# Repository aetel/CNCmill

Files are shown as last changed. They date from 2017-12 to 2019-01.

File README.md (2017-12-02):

# CNCmill
CNC mill based on the Sienci Mill One

## AETEL version

Frame has been modified to be cut from 4mm steel

## Shoulder of giants

The Mill One utilizes the following open-source projects:

-> GRBL firmware

"GRBL is opensource software that runs on an Arduino Uno that takes G-Code commands via Serial and turns the commands into motor signals."
https://github.com/grbl/grbl

-> Arduino Uno

"The Arduino Uno is a micro-controller board based on the ATmega328. It has 14 digital input/output pins (of which 6 can be used as PWM outputs), 6 analog inputs, a 16 MHz ceramic resonator, a USB connection, a power jack, an ICSP header, and a reset button. It contains everything needed to support the micro-controller; simply connect it to a computer with a USB cable or power it with a AC-to-DC adapter or battery to get started."
http://www.arduino.org/products/boards/arduino-uno

-> Arduino IDE

"The open-source Arduino Software (IDE) makes it easy to write code and upload it to the board. It runs on Windows, Mac OS X, and Linux. The environment is written in Java and based on Processing and other open-source software."
https://www.arduino.cc/en/main/software

-> CNC V3.0 HCARDU0086 Arduino Shield

"This shield (HCARDU0086) is designed to allow you to control a CNC router or milling machine from an Arduino board. It contains 4 driver sockets which allows compatible Pololu A4988 driver modules to be inserted (see HCMODU0068 on our website) providing the ability to drive 3 stepper motor axis (X,Y, & Z) plus an optional 4th auxiliary motor. Additional connectors provide easy connection of end stop sensors and control buttons."
http://forum.hobbycomponents.com/viewtopic.php?f=40&t=1747
http://blog.protoneer.co.nz/arduino-cnc-shield/

-> Pololu A4988 stepper motor drivers

"This breakout board for Allegro’s A4988 microstepping bipolar stepper motor driver features adjustable current limiting, over-current and over-temperature protection, and five different micro-step resolutions (down to 1/16-step). It operates from 8 V to 35 V and can deliver up to approximately 1 A per phase without a heat sink or forced air flow (it is rated for 2 A per coil with sufficient additional cooling)."
https://www.pololu.com/product/1182

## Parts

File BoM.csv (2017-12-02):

Quantity | Item | Notes | Inventory | Total Part Count | This BOM may change at any time
 |  |  |  | 197 | Sienci Mill One V1
4 | Frame (MDF) | One set
2 | 2" x 2" x 1/4" Aluminum Rail (400mm)
1 | 2" x 2" x 1/4" Aluminum Rail (200mm)
1 | Acrylic Shield
1 | X/Z Gantry
1 | Y Gantry
3 | NEMA 17 | 1.5A or better
12 | Delrin V Wheels
6 | M5 Eccentric Nuts | M5 tapped hole
3 | 5mm to 8mm solid coupler
1 | 24V Power Supply (Brick) | 5A or better
1 | AC Power Cable | Compatible with power supply
3 | ACME Leadscrew Nuts | Brass, for 8mm leadscrew
2 | 400mm ACME Lead Screw
1 | 200mm ACME Lead Screw
3 | Stepper driver chips (A4988 or DRV8825) | matched to NEMA 17 motors
1 | CNC V3 Shield
1 | Arduino Uno
1 | USB Cable
1 | DC Power Plug
1 | DC Power Cable
6 | Header Jumpers
26 | M8 - 25mm Socket Head
26 | M8 Hex Nuts
12 | M8 - 15mm Socket Head
16 | M5 - 25mm Socket Head
12 | M5 Washer
10 | M5 Hex Nuts
12 | M3 - 8mm Socket Head
6 | M3 - 15mm Socket Head
6 | M3 Hex Nuts
3 | ACME nut holder | 3D printed
5 | Angle mount | 3D printed
1 | Electronics case | 3D printed
1 | Router mount | 3D printed
4 | Frame brackets | 3D printed
1 | 5V 2 pin 40mm fan | Optional

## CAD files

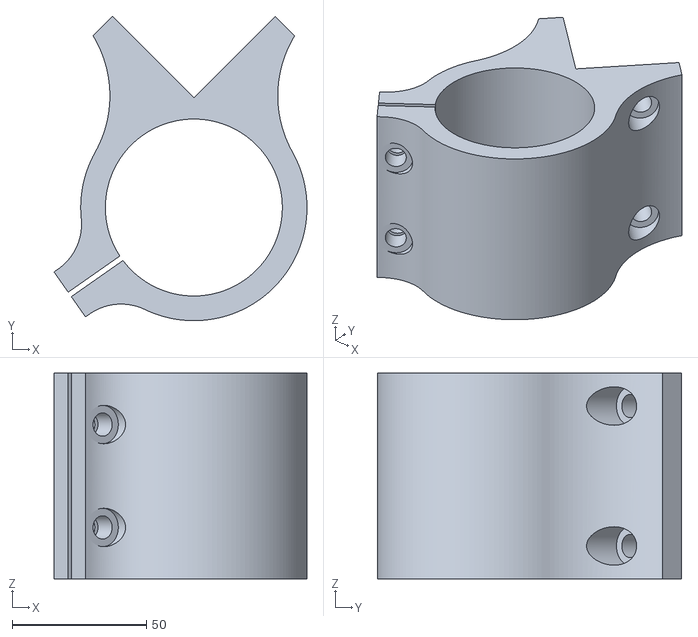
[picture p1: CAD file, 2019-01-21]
3Dprint/Makita-Ridgid Router Mount.stl
94.1 x 113.2 x 76.5

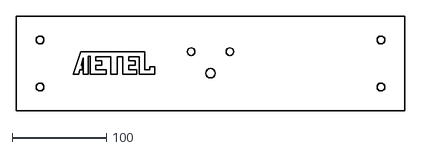
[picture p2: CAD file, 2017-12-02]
cut/steel/frame/front_aetel.dxf
412.7 x 100.0

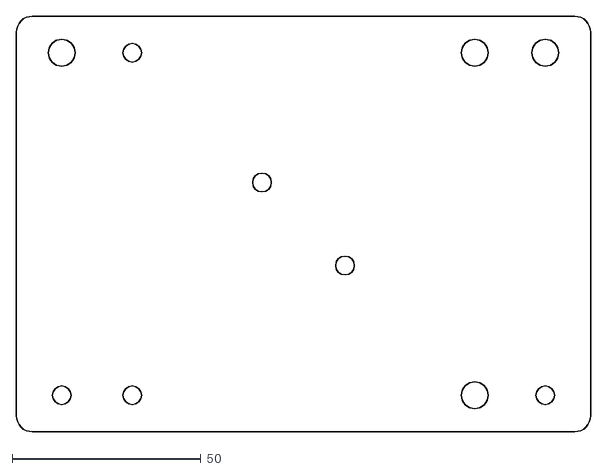
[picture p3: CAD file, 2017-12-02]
cut/steel/XZ_gantry.dxf
152.0 x 110.0

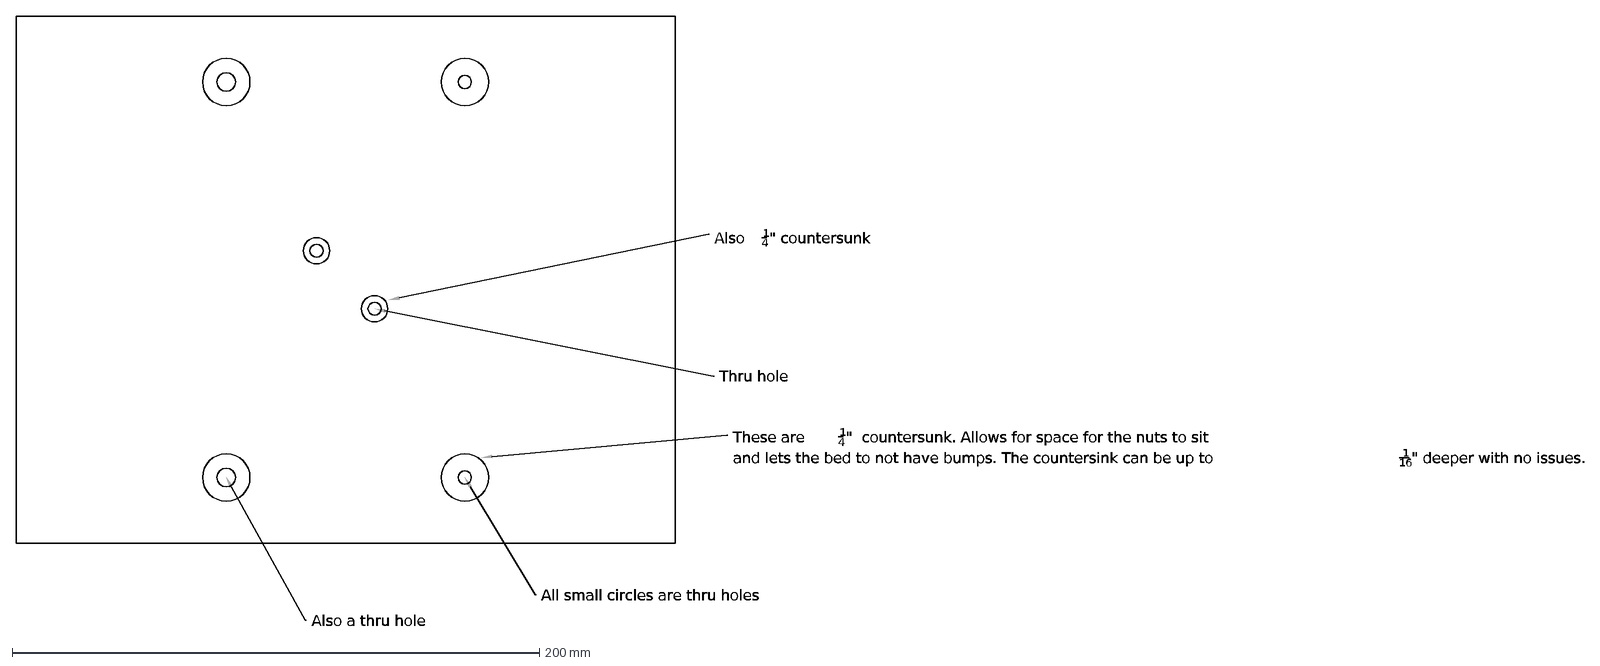
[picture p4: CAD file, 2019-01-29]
cut/wood/20x25/Y_Gantry.dxf
All small circles are thru holes
Also a thru hole
These are
1
4
" countersunk. Allows for space for the nuts to sit
and lets the bed to not have bumps. The countersink can be up to
16
" deeper with no issues.
Also
" countersunk
Thru hole

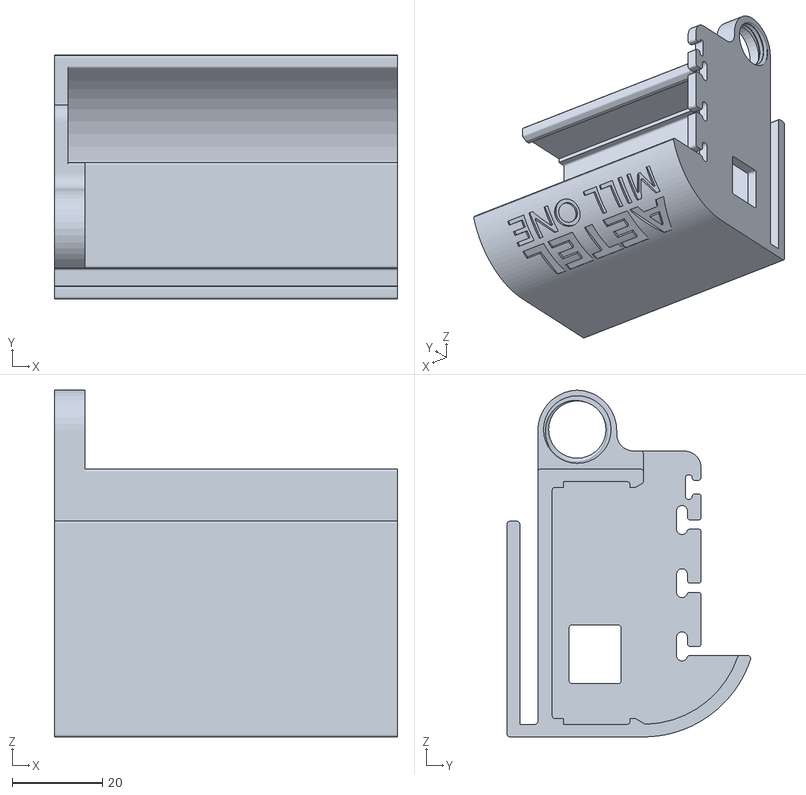
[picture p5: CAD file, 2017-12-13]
3Dprint/AETEL_Electronics_enclosure.stl
76.0 x 54.0 x 76.8

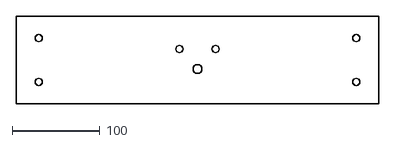
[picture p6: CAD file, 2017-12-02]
cut/steel/frame/front.dxf
412.7 x 100.0

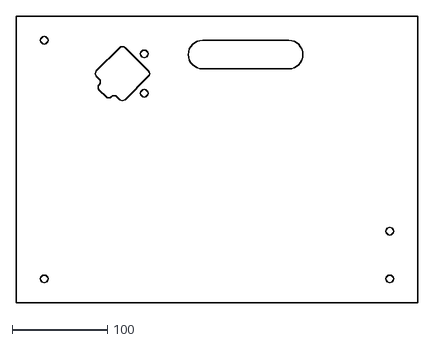
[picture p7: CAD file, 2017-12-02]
cut/steel/frame/right.dxf
420.3 x 300.0

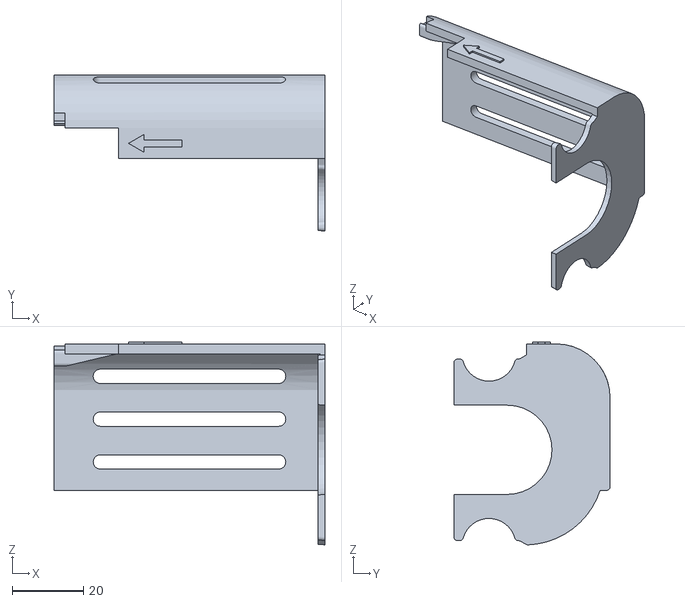
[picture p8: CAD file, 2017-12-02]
3Dprint/Sienci_Mill_One_V2_Electronics_enclosure_cover.STL
76.0 x 43.8 x 56.9

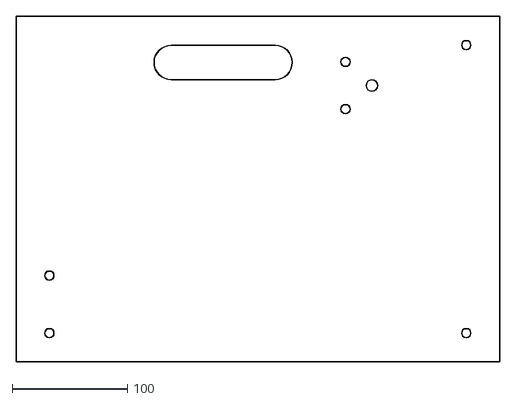
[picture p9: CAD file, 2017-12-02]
cut/steel/frame/left.dxf
420.3 x 300.0

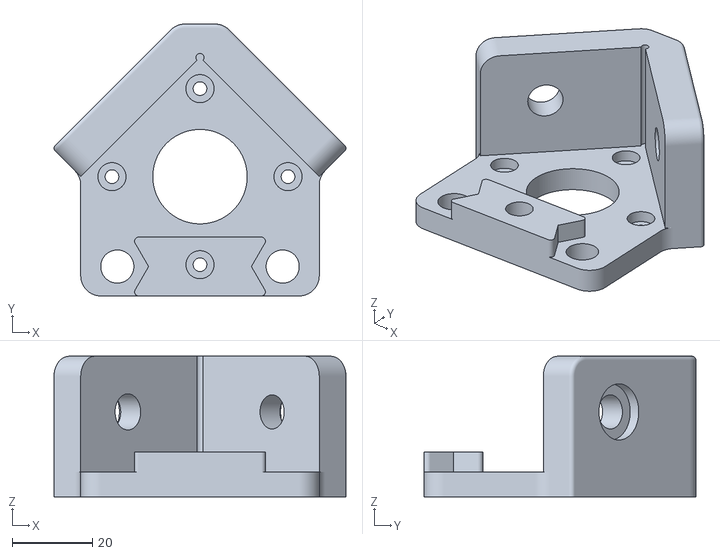
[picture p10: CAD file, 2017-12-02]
3Dprint/Sienci_Mill_One_V2_Angle_Bracket.stl
72.7 x 67.7 x 35.0

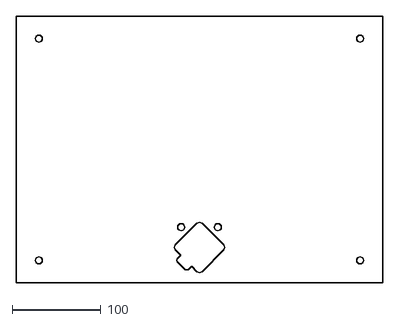
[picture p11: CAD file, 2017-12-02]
cut/steel/frame/back.dxf
412.7 x 300.0

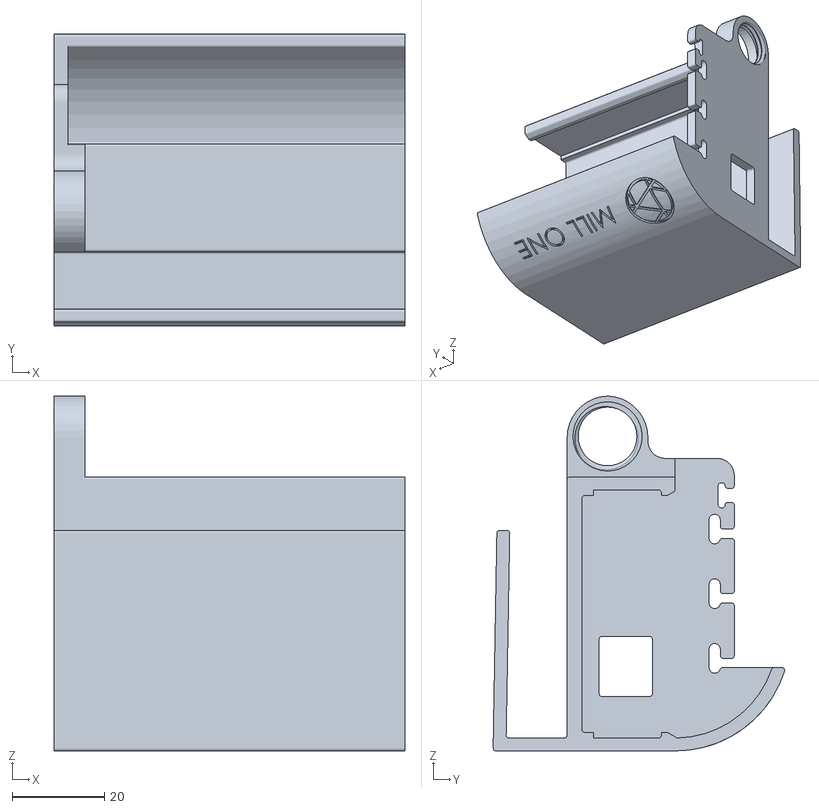
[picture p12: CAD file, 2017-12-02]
3Dprint/Sienci_Mill_One_V2_Electronics_enclosure.STL
76.0 x 63.1 x 76.8

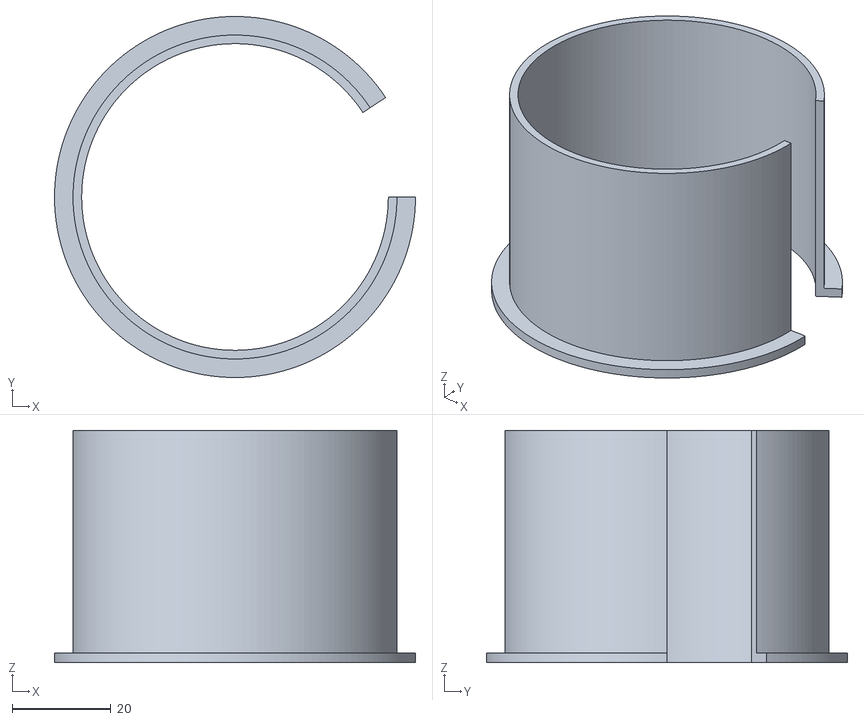
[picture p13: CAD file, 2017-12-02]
3Dprint/Sienci_Mill_One_V2_Ridgid_bushing.stl
73.0 x 73.0 x 47.0

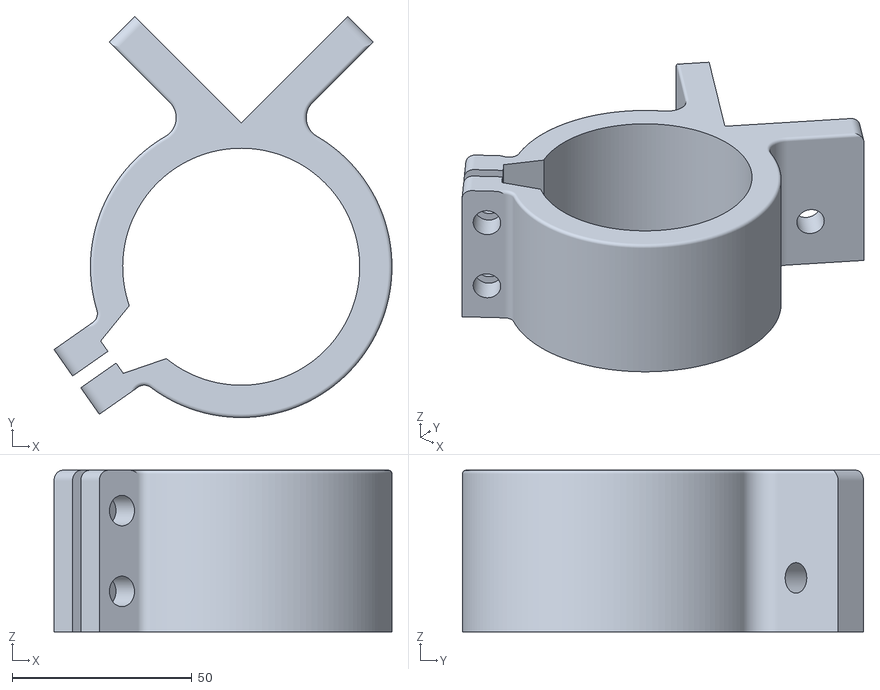
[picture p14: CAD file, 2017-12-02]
3Dprint/Sienci_Mill_One_V2_Makita-Ridgid_Router_Mount.stl
94.1 x 111.7 x 45.0

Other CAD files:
3Dprint/Sienci_Mill_One_V2_ACME_Nut_Mount.stl

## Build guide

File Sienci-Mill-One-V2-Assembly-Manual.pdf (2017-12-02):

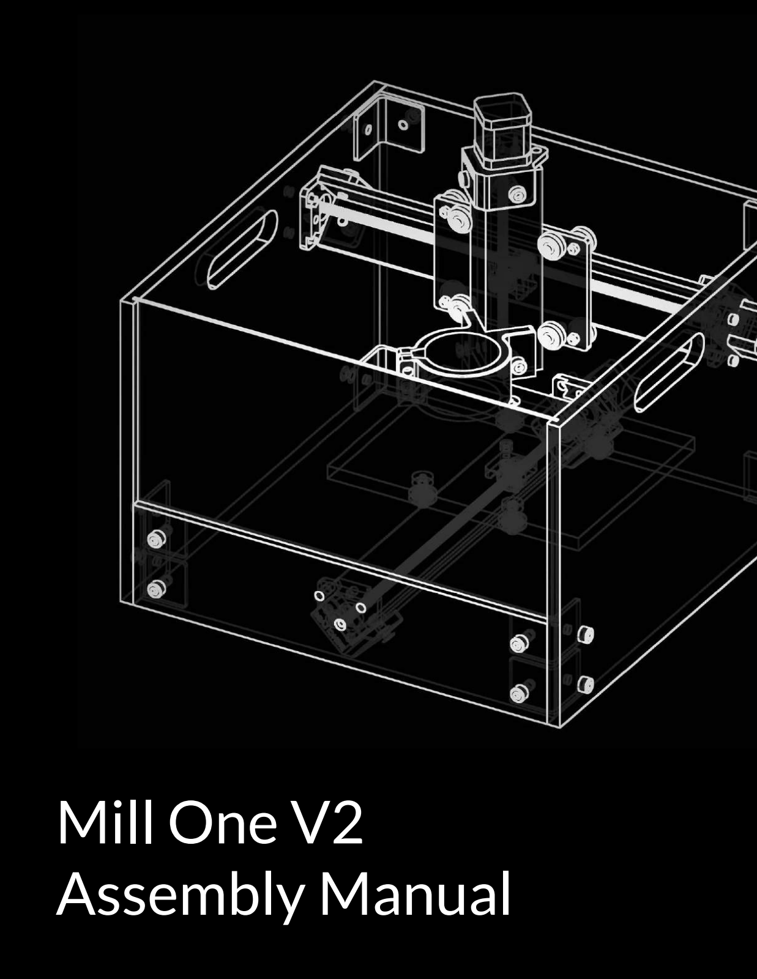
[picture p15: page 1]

# Mill One V2 Assembly Manual

Throughout this policy the words "we", "us" and "our", or “Sienci Labs” will be used to refer to Sienci Labs Inc. herein and “Mill One” or “machine” will refer to Sienci Labs’ Sienci Mill One product. Additionally, the words "you", "your", “user”, and “operator” will refer to the original purchaser/customer, user, or viewer of any of the products or media provided by or through Sienci Labs.

Machine Disclaimer

The listed “Safety Warnings and Guidelines” outline the necessary precautions that should be taken any time the machine is operated. By assembling our provided kit, the product user takes on all the associated liability pertaining to the operation and maintenance of the Mill One. Sienci Labs will not be held responsible for any damages to property or injury incurred on the operator or bystanders if any alterations are made to the design or assembly of our machine. Although care is taken to ensure the accuracy of information made available on our website (www.Sienci.com) and other forms of media, Sienci Labs will not be held liable for any inaccuracies, errors, or inconsistencies in website content, the content of files linked to by our website, references made to external websites herein, and/or other information produced by Sienci Labs. The information which has been made available will not be applicable to all situations and is subject to change without notice so it should not substitute for the discretion of the user. Variability in machine accuracy and performance may occur due to improper machine assembly by the user, as such, Sienci Labs takes on no responsibility for variation between claimed machine specifications and the performance of the user’s machine from improper assembly.

Safety Warnings and Guidelines

1. Be sure to carefully follow provided machine assembly instructions before machine use to ensure operator safety.
2. All wires must be appropriately positioned before beginning the operation of this machine. Cutting a “live” wire may cause exposed metal parts of the routing/trimming tool to become electrified and shock the operator.
3. Ensure the machine is placed on a flat surface and in a well-ventilated space before operation.
4. Always wear eye protection during machine operation.
5. Always wear hearing protection during extended machine operation based on proximity to machine.
6. Materials may release chemicals that are toxic or unsafe to inhale when cut. Always check the Material Safety Data Sheet (MSDS) of the material in question before cutting. Always cover exposed skin and wear appropriate airway protection (e.g. dust mask/respirator) specific to the material used and its application.
7. Any workpiece must be appropriately secured before starting a cutting routine by clamps or other practical securing method. Holding the material by hand or employing any any other unstable form of securing will lead to unsafe loss of machine control.
8. Cutting bits used for the Mill One should be used at the discretion of the user. Bits are sharp and can crack and break without notice so appropriate care should be taken by the user while manipulating and installing them. Carefully check bits for cracks or damage before operating the machine and replace any cracked or unfit bits immediately.
9. Carefully inspect any consumable material before use on the machine, any unforeseen inconsistency in material hardness or material quality may cause damage to the machine.
10. Keep away from all moving parts during machine operation.
11. Before beginning a cutting job, ensure the router/trimmer runs properly. Immediately disable the tool if visible vibration or wobble occurs. This might indicate a damaged tool or an improperly installed bit.
12. Make sure the bit is not contacting the workpiece before the router/trimmer tool is turned on.
13. Do not leave the machine running unattended, the machine should only be operated with the operator present.
14. Do not touch the cutting bit immediately after use. It may be hot and could burn the operator.
15. Use bits that are appropriate to the material and cutting speed used.

## LIST OF PARTS

## STEP 1

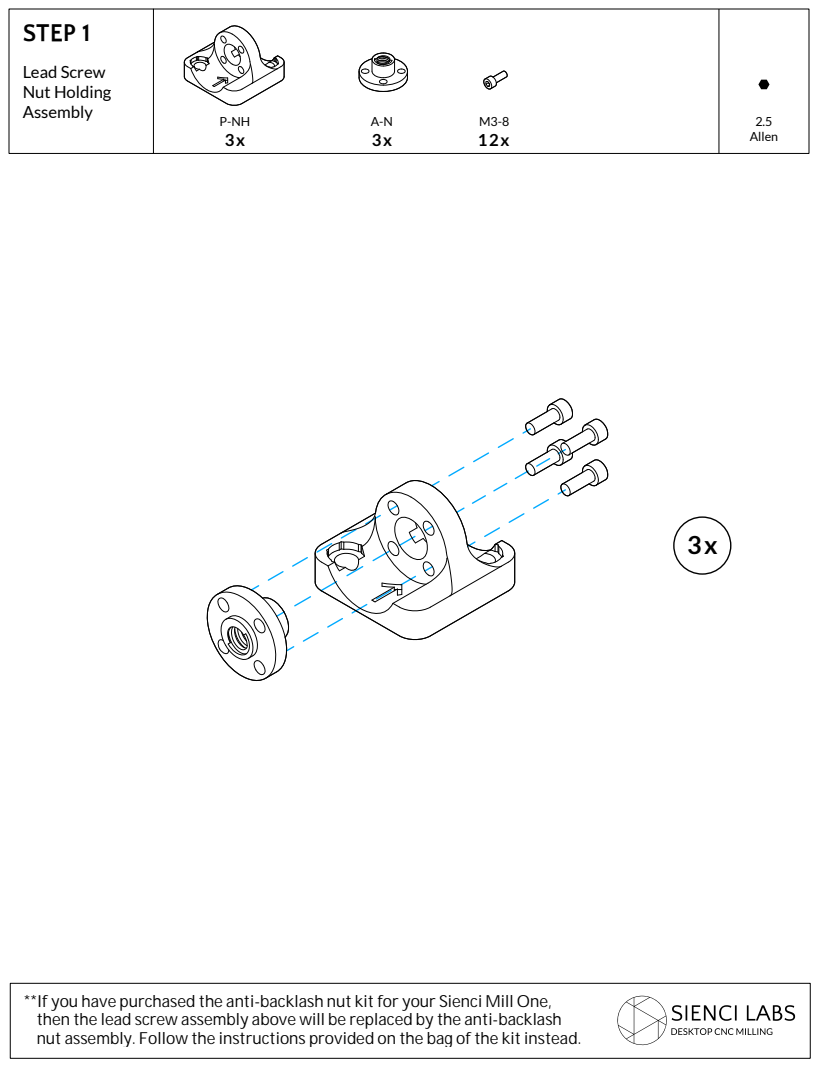
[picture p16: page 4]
Lead Screw Nut Holding Assembly; 2.5 Allen

## STE

P 2

## STE

P 3

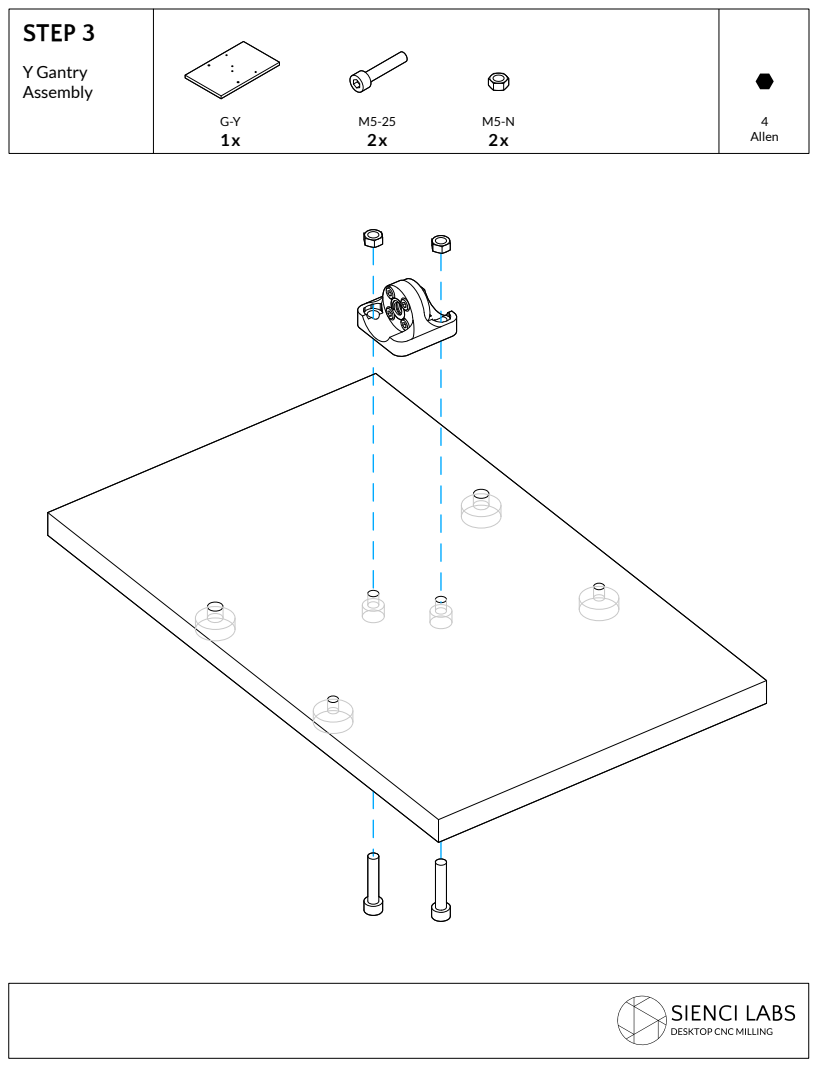
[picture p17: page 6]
Y Gantry Assembly; 4 Allen

## STEP 4

Match the eccentric nuts (M5-NE)
to the larger holes, and the regular
nuts (M5-N) to the smaller holes

## STEP 5

!

Match the eccentric nuts (M5-NE) to the larger
holes, and the regular nuts (M5-N) to the smaller
holes

## STEP 6

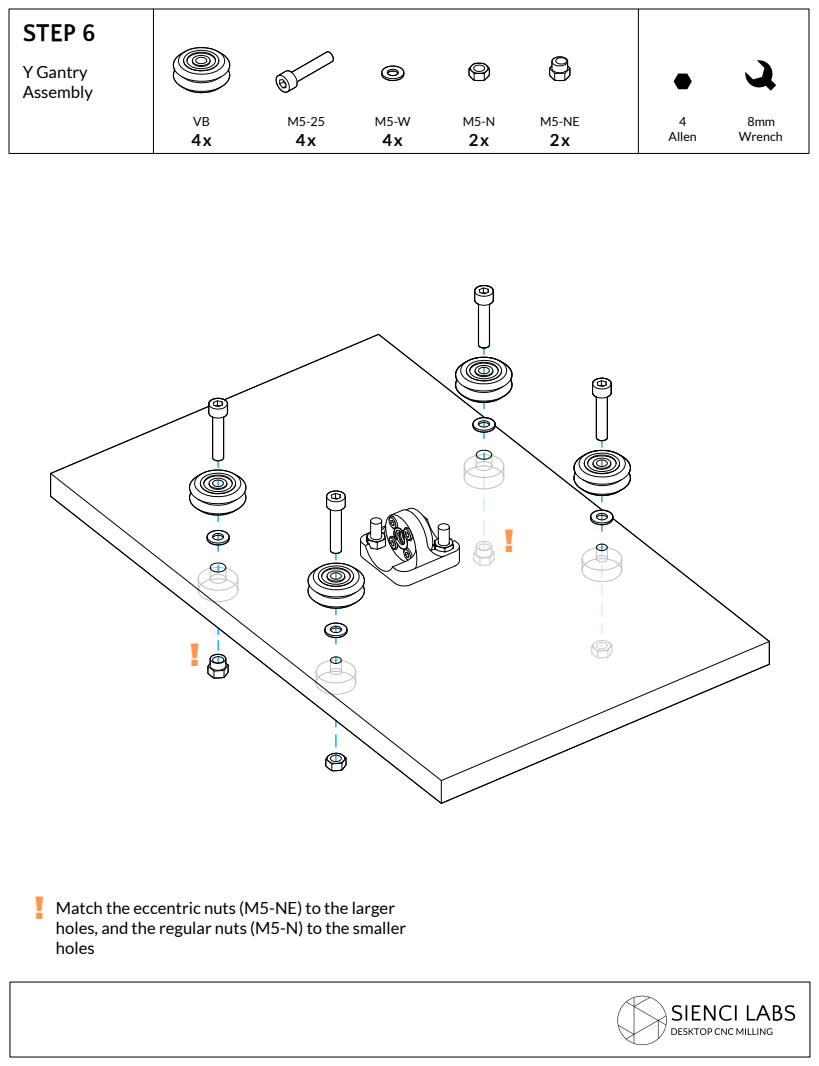
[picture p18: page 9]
Y Gantry Assembly; Allen; Wrench

Match the eccentric nuts (M5-NE) to the larger
holes, and the regular nuts (M5-N) to the smaller
holes

## STEP 7

Mounting the
Motors to the
Rails

Make sure that the motor connector is facing
downwards

## STEP 8

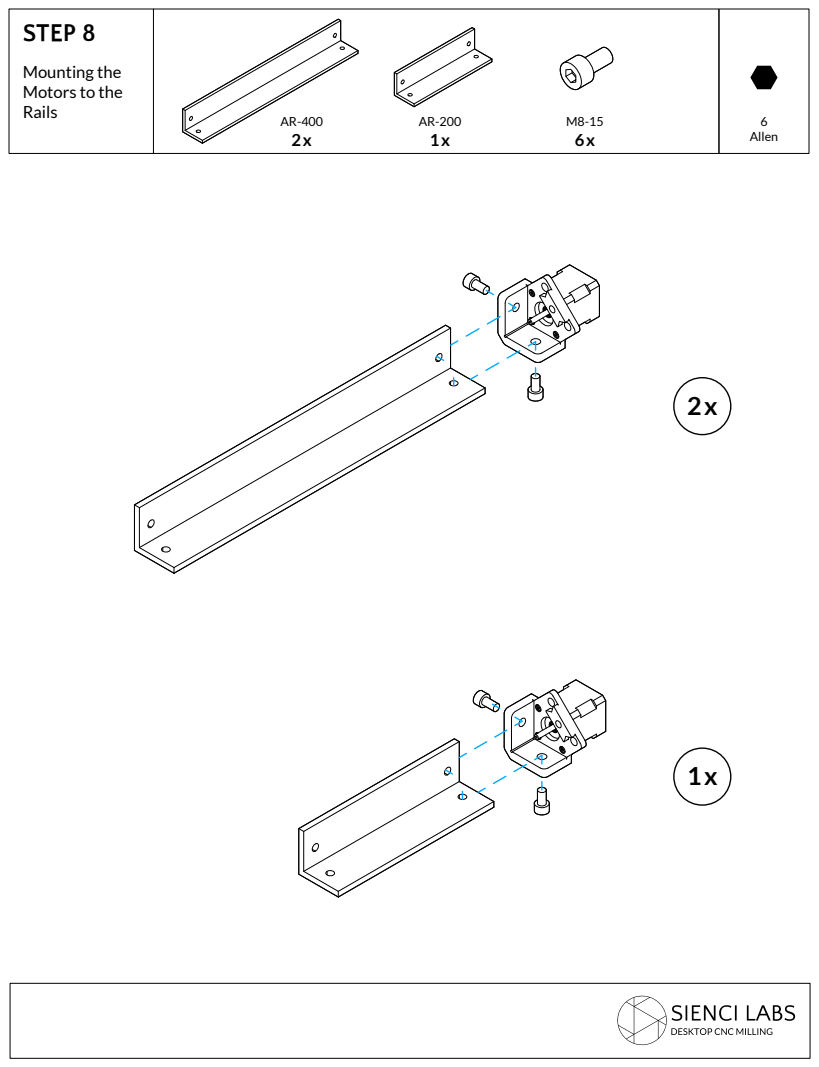
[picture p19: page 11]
6 Allen

Mounting the
Motors to the
Rails

## STEP 9

! Make sure to push coupler all the way onto lead
screw before tightening

## STEP 10

Attaching the
Z-Rail to the XZ
Gantry

Rotate the eccentric nuts (M5-NE)
until gantry slides onto the rail easily

Make sure to push coupler all the way onto
motor shaft before tightening

## STEP 11

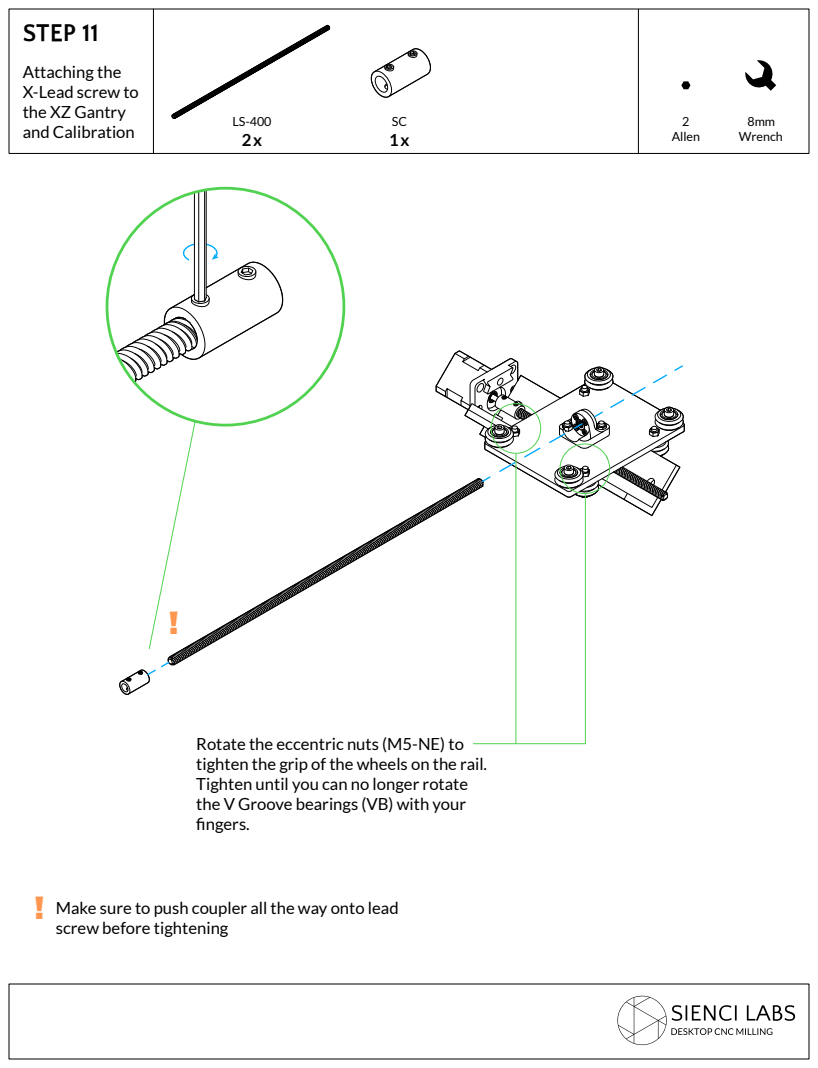
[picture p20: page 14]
the XZ Gantry; and Calibration; Allen; Wrench

Attaching the
X-Lead screw to

Rotate the eccentric nuts (M5-NE) to
tighten the grip of the wheels on the rail.
Tighten until you can no longer rotate
the V Groove bearings (VB) with your
fingers.

! Make sure to push coupler all the way onto lead
screw before tightening

## STEP 12

Attaching the
X-Rail to the XZ
Gantry

Rotate the eccentric nuts (M5-NE)
until gantry slides onto the rail easily

Make sure to push coupler all the way onto
motor shaft before tightening

## STEP 13

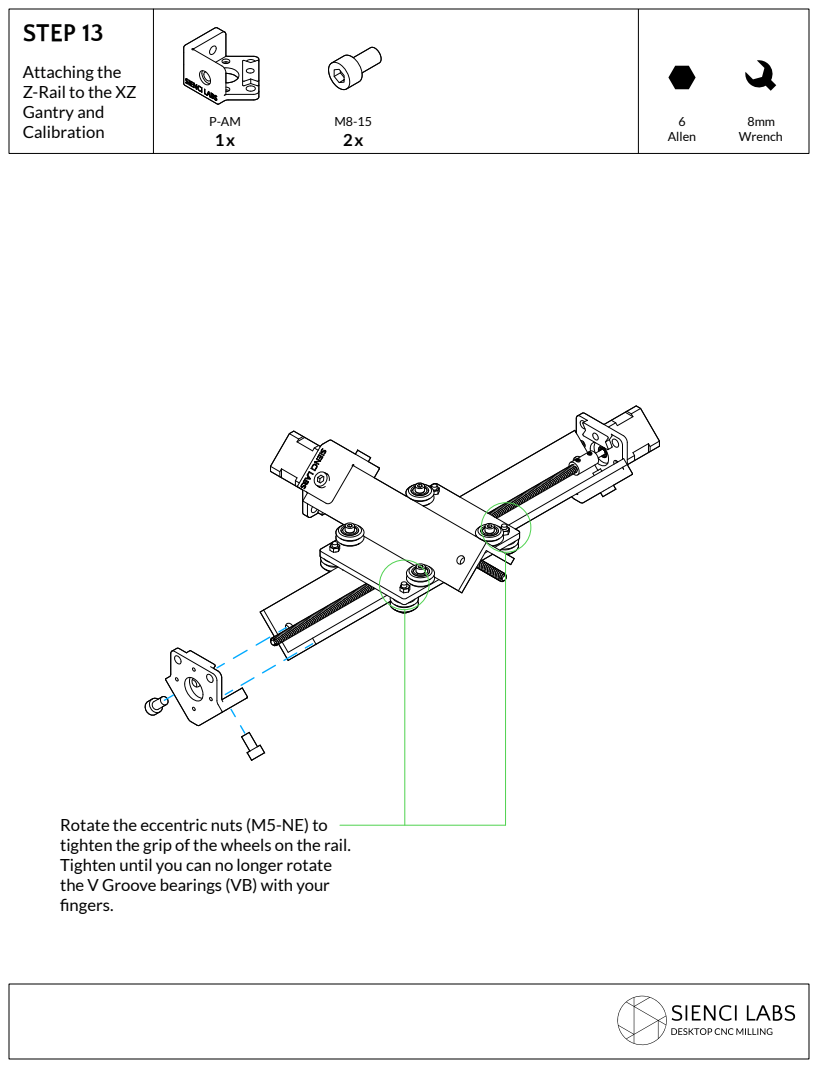
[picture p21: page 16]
Wrench; Gantry and; 6 Allen; Calibration

Attaching the
Z-Rail to the XZ

Rotate the eccentric nuts (M5-NE) to
tighten the grip of the wheels on the rail.
Tighten until you can no longer rotate
the V Groove bearings (VB) with your
fingers.

## STEP 15

Make sure to push coupler all the way onto lead
screw before tightening

## STEP 15

Attaching the
Y-Rail to the Y
Gantry

Rotate the eccentric nuts (M5-NE)
until gantry slides onto the rail easily

Make sure to push coupler all the way onto
motor shaft before tightening

## STEP 16

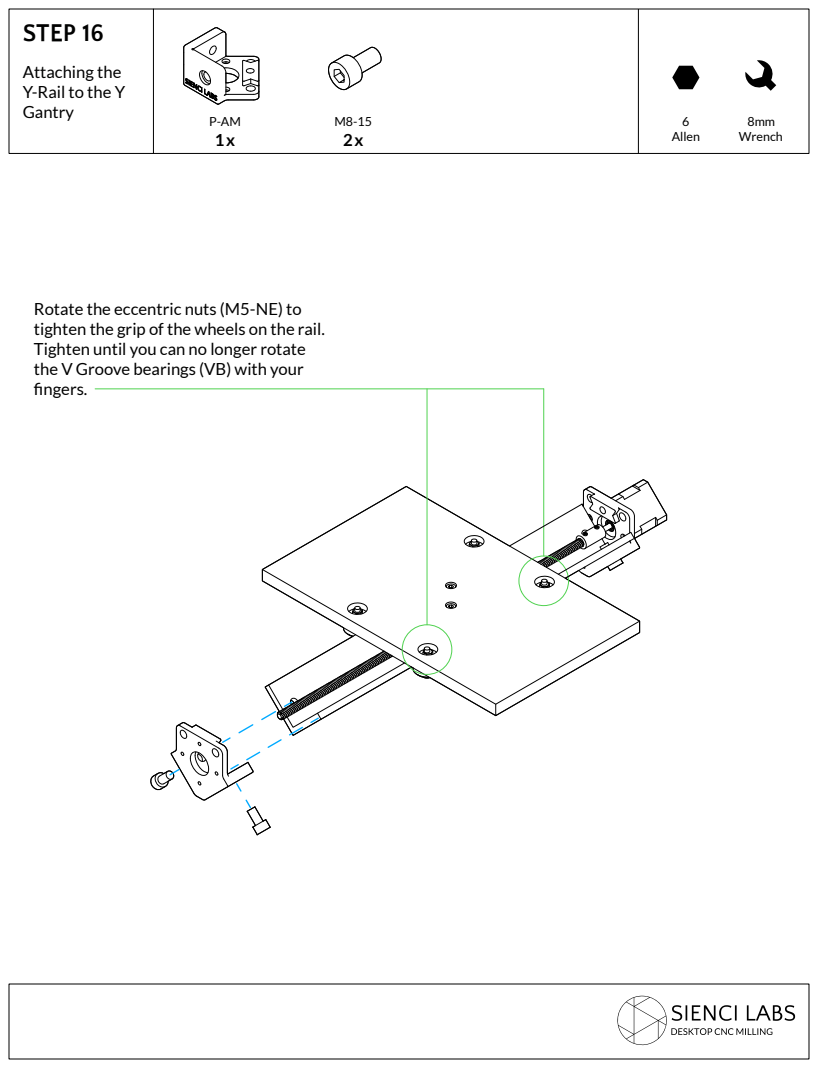
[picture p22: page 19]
Wrench; 6 Allen

Attaching the
Y-Rail to the Y
Gantry

Rotate the eccentric nuts (M5-NE) to
tighten the grip of the wheels on the rail.
Tighten until you can no longer rotate
the V Groove bearings (VB) with your
fingers.

## STE

P 17

## STE

P 18

## STEP 19

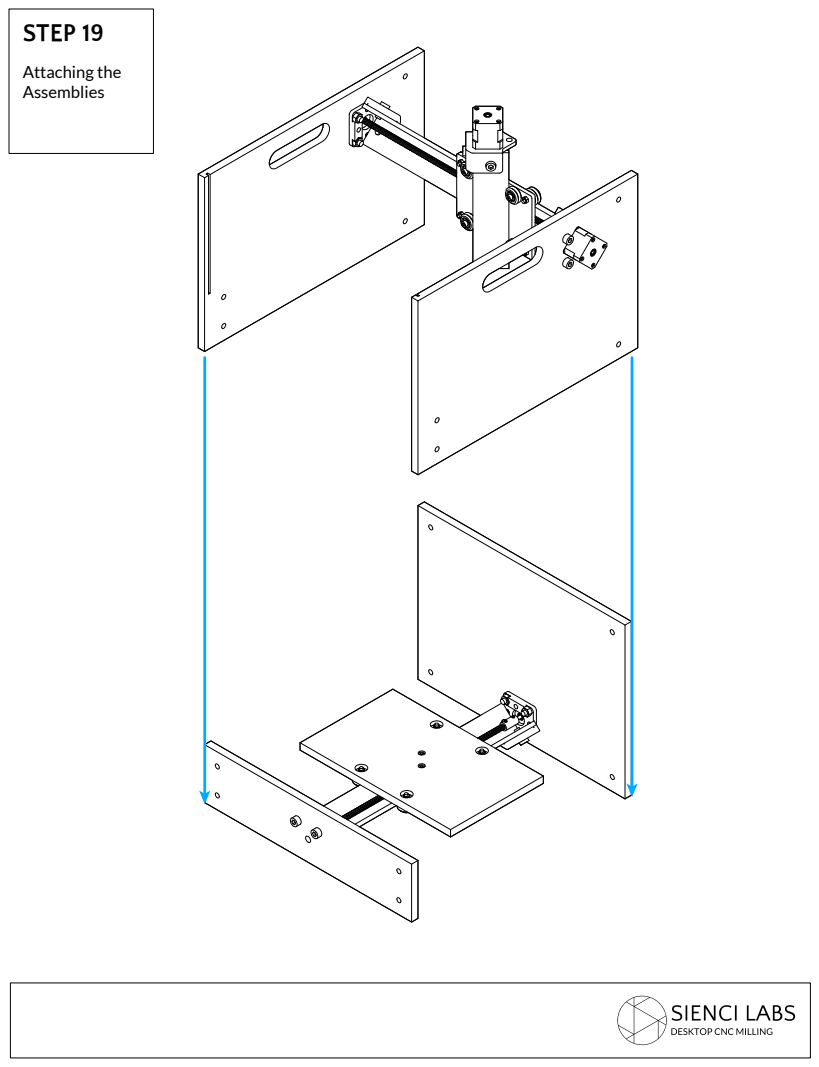
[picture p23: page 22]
Attaching the Assemblies

## STEP 20

Twist on bolts on all corners loosely,
then tighten on a flat surface

## STE

P 21

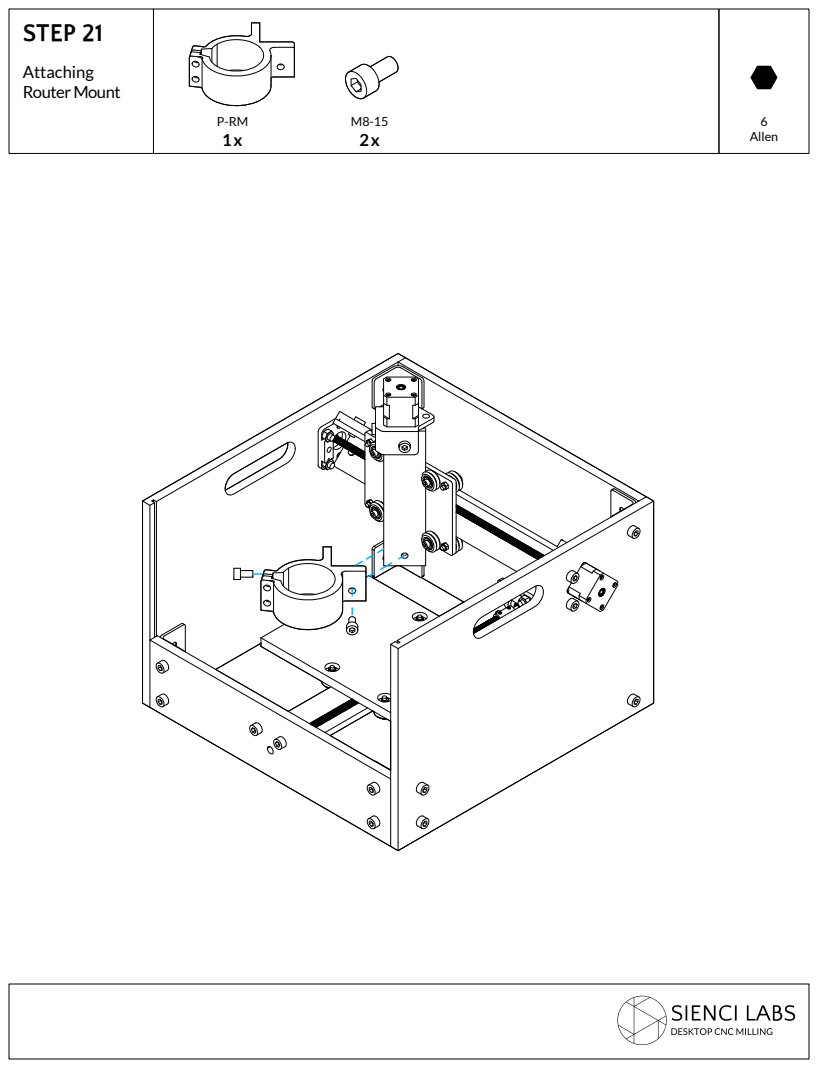
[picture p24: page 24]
Attaching Router Mount; 6 Allen

## STEP 22

P-RM router mount fits the Makita
RT0701 router without P-RB bushing,
bushing only required to mount
Ridgid R24012 router

## STE

P 23

## STE

P 24

## STE

P 25

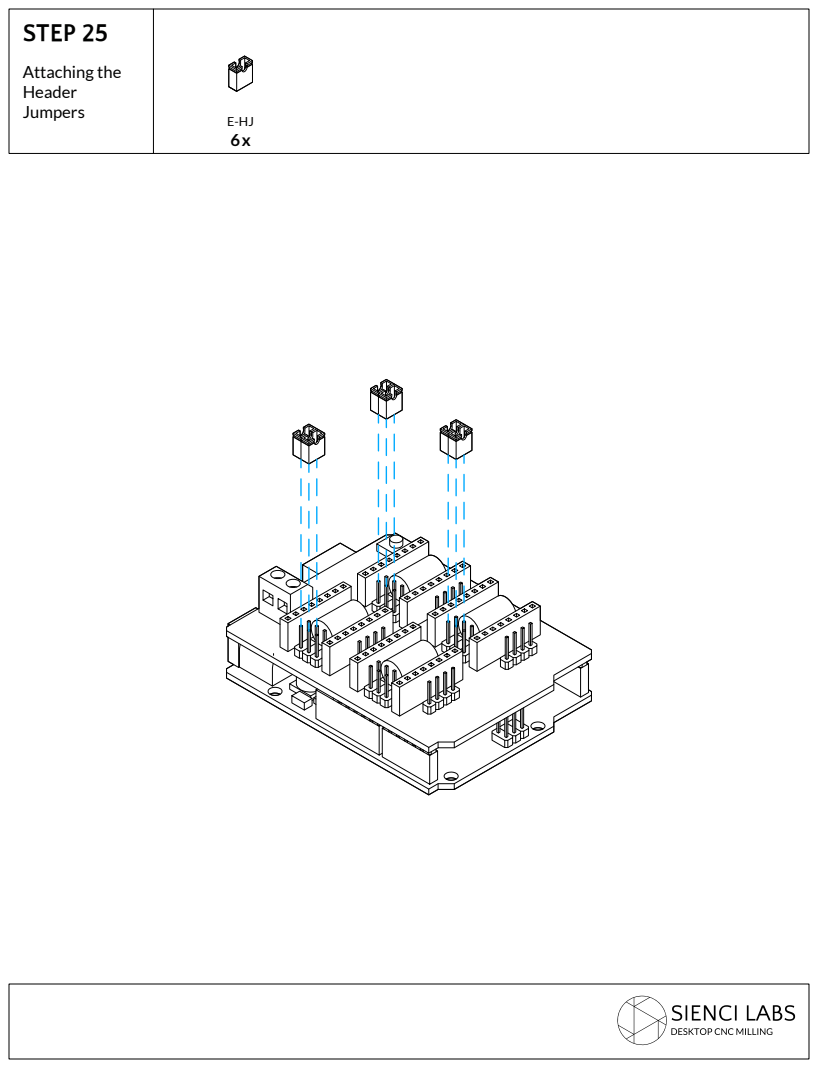
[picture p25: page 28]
Attaching the Header; Jumpers

## STEP 26

Z | X | Y

! Make sure the black wire is oriented as depicted

## STEP 27

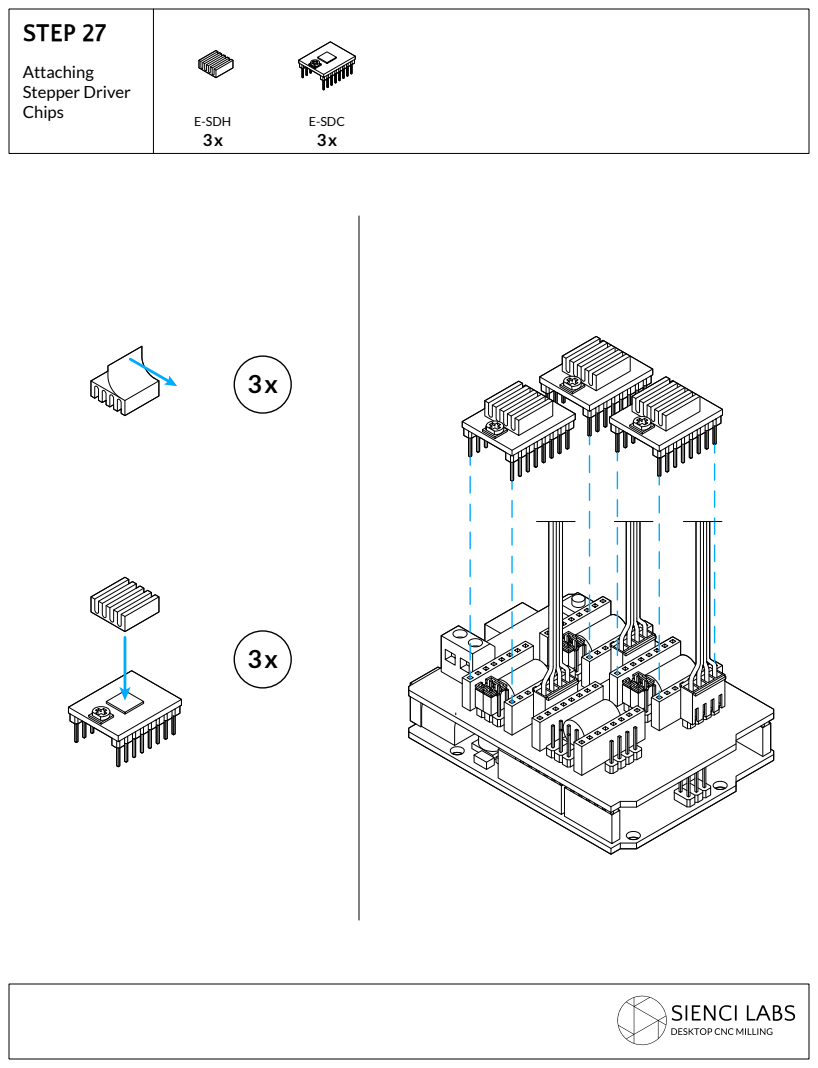
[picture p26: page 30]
Attaching Stepper Driver Chips; E-SDH 3x; E-SDC 3x

## STEP 28

Tuning the
Stepper Motor
Drivers

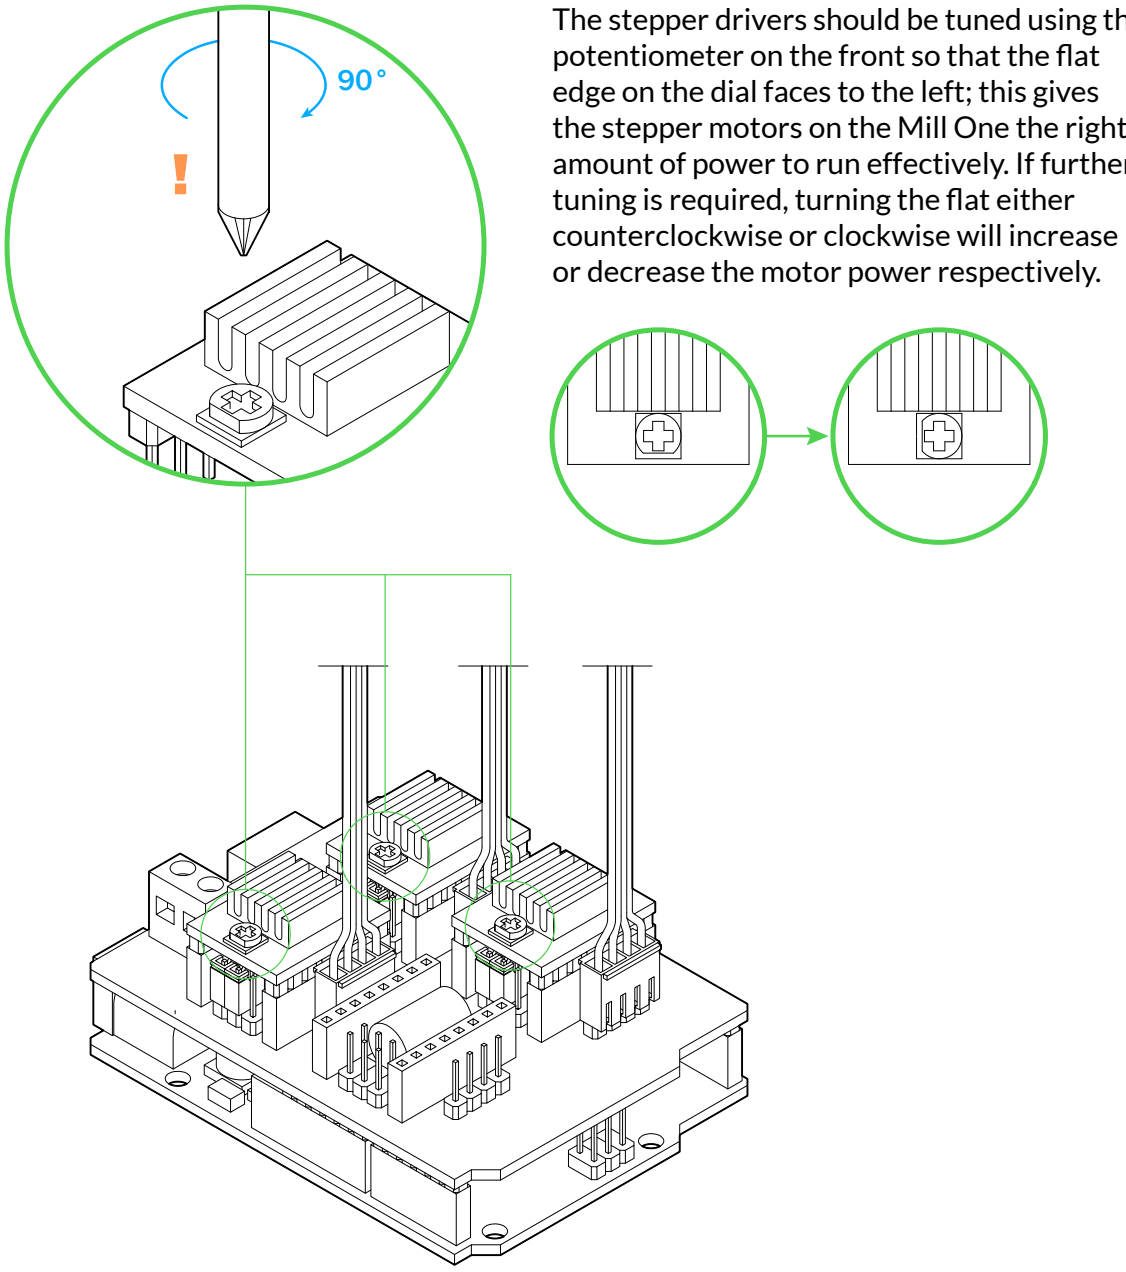
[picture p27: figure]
counterclockwise or clockwise will increase

! Stepper driver potentiometers should never

be turned while the board is powered up

The stepper drivers should be tuned using the potentiometer on the front so that the flat edge on the dial faces to the left; this gives the stepper motors on the Mill One the right amount of power to run effectively. If further tuning is required, turning the flat either

or decrease the motor power respectively.

Phillips

## STE

P 29

## STEP 30

## STEP 31

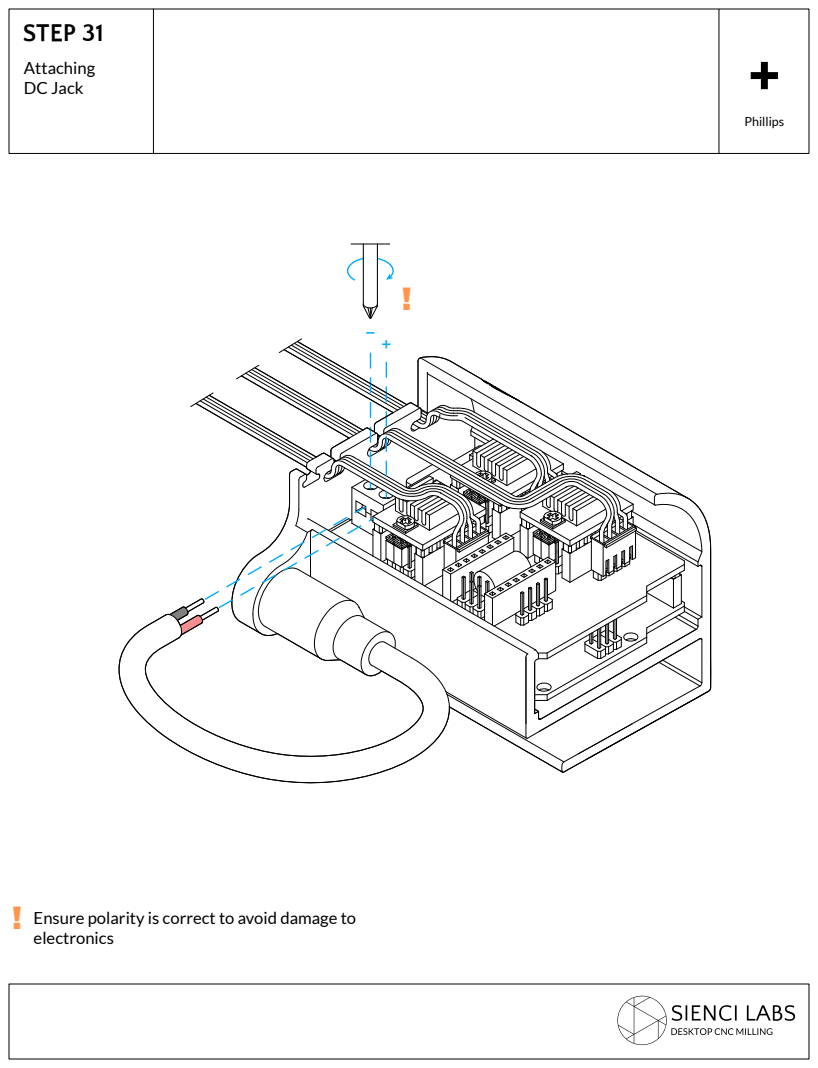
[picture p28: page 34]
Attaching DC Jack; Phillips

! Ensure polarity is correct to avoid damage to
electronics

## STEP 32

## STEP 33

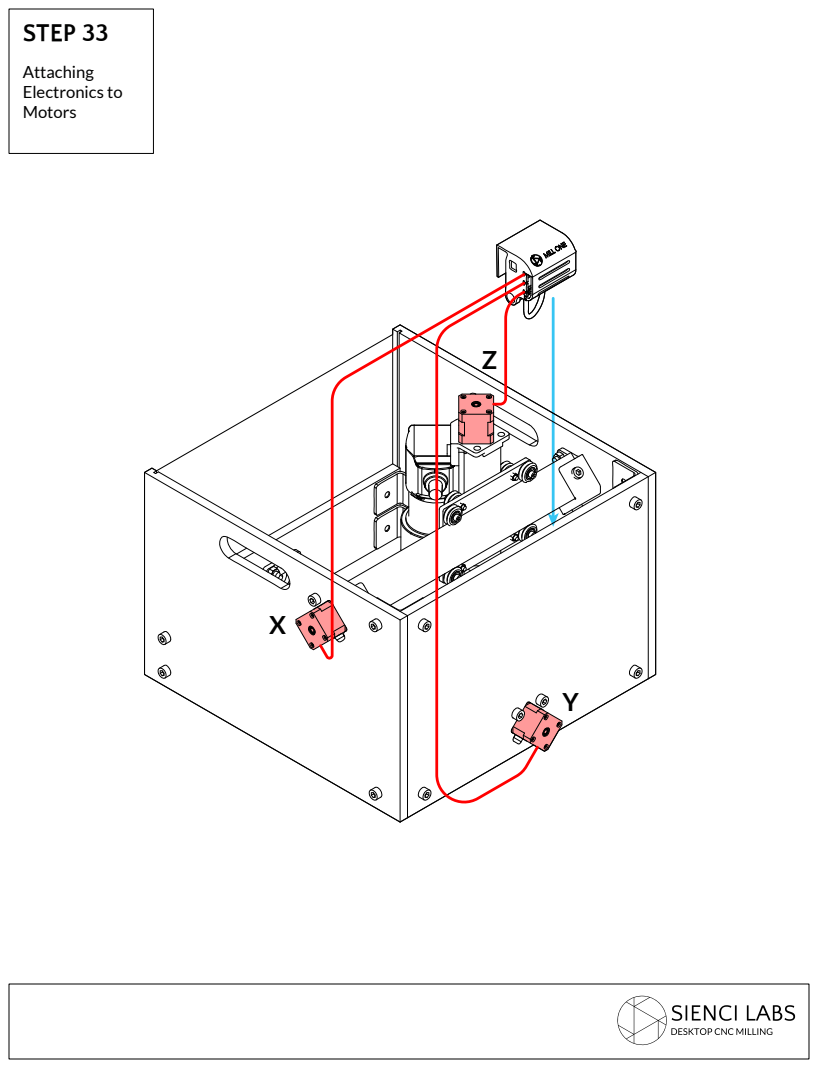
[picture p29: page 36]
Attaching Electronics to Motors

## STEP 34

Your Mill One is now fully assembled. Don’t plug in your power brick yet, simply
connect the USB cable to your computer and continue onto the next steps.

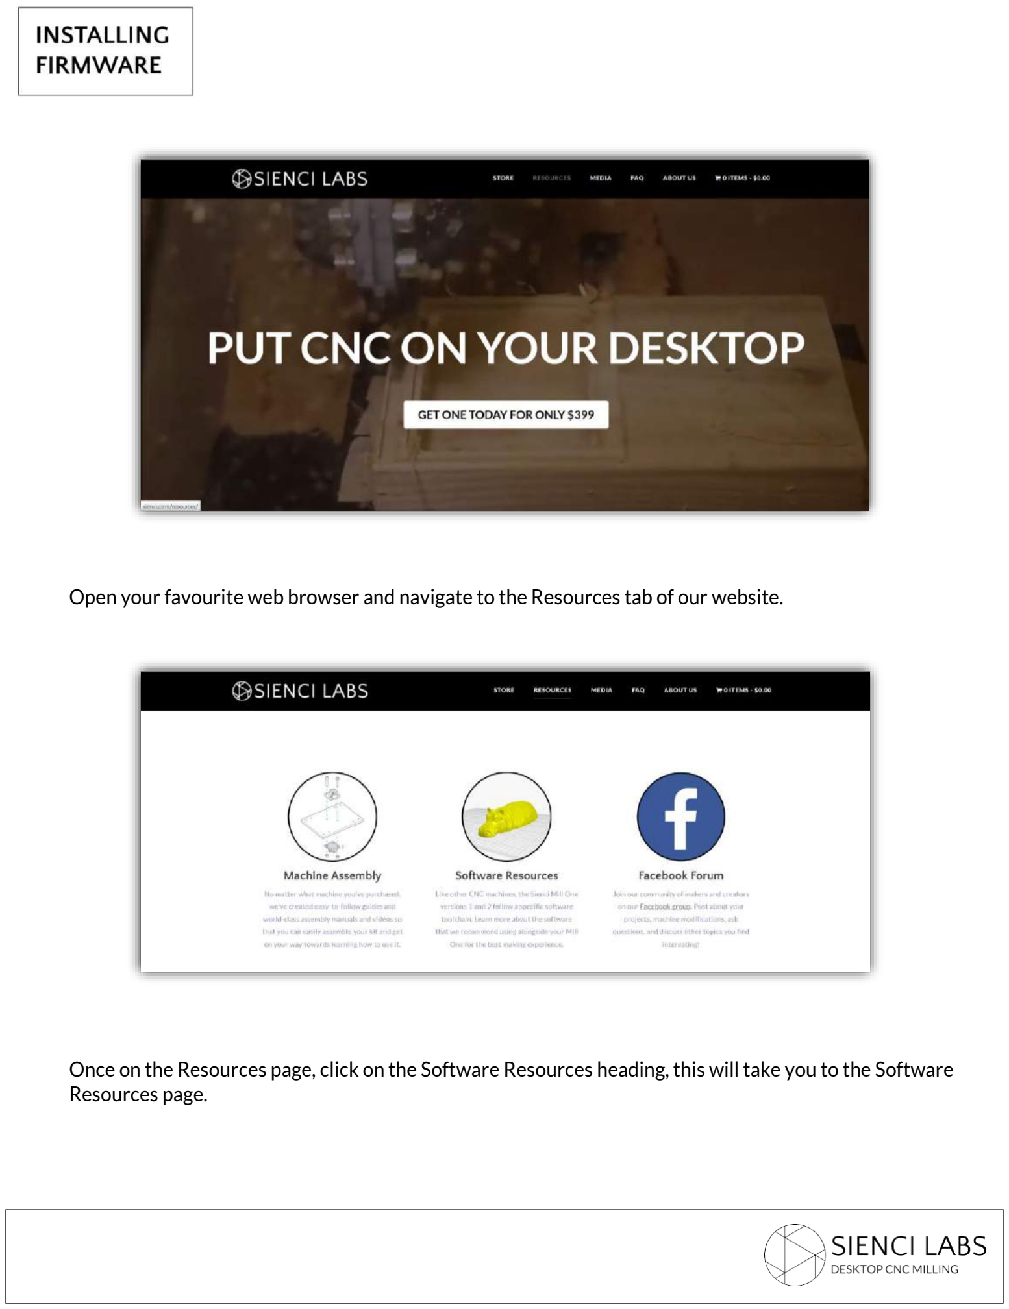
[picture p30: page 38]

Open your favourite web browser and navigate to the Resources tab of our website.

Once on the Resources page, click on the Software Resources heading, this will take you to the Software Resources page.

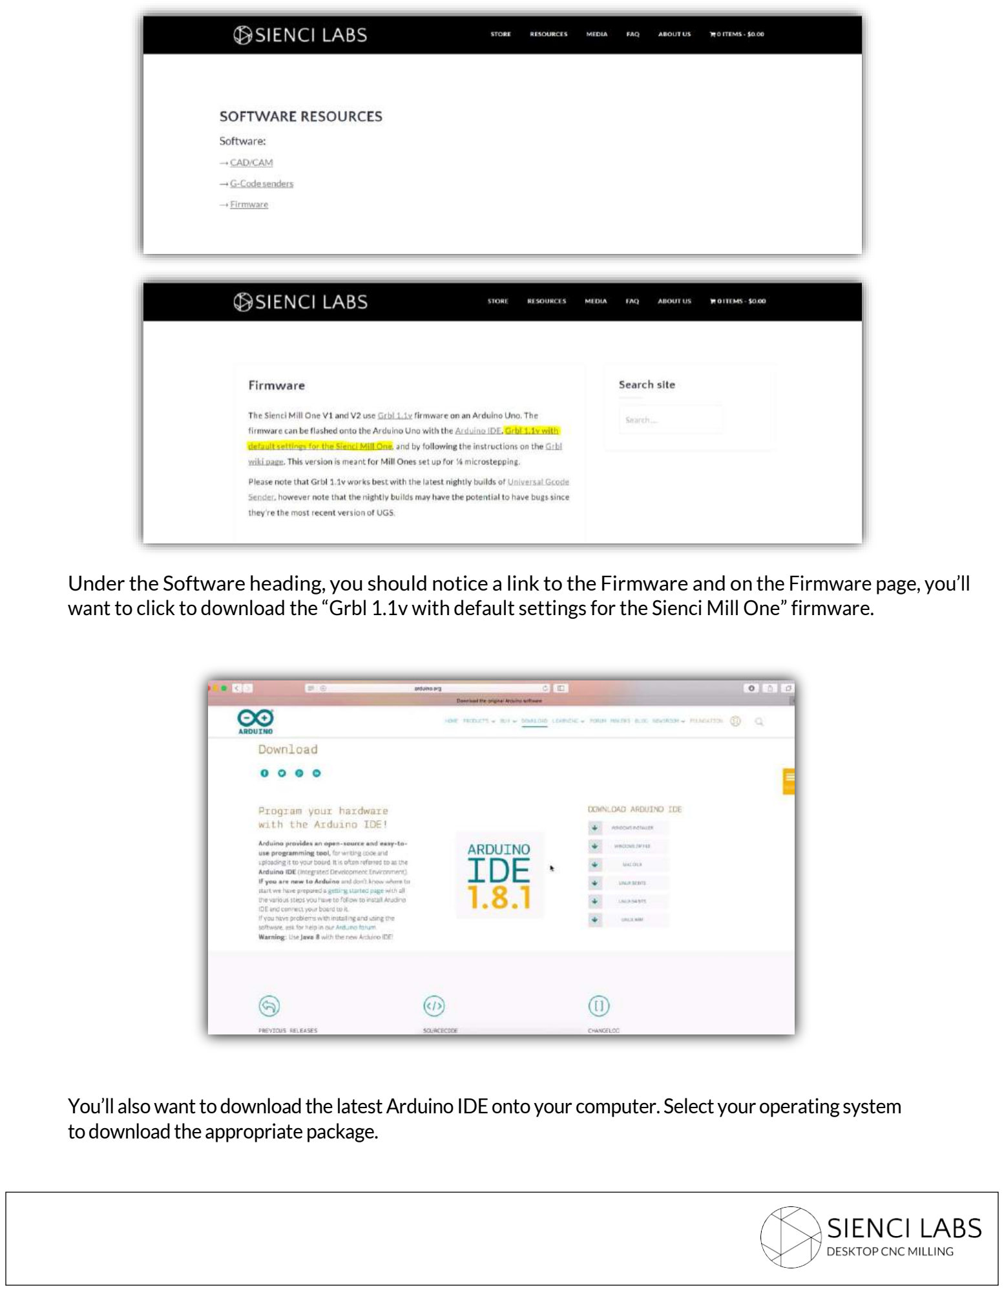
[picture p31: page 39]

Under the Software heading, you should notice a link to the Firmware and on the Firmware page, you’ll want to click to download the “Grbl 1.1v with default settings for the Sienci Mill One” firmware.

You’ll also want to download the latest Arduino IDE onto your computer. Select your operating system to download the appropriate package.

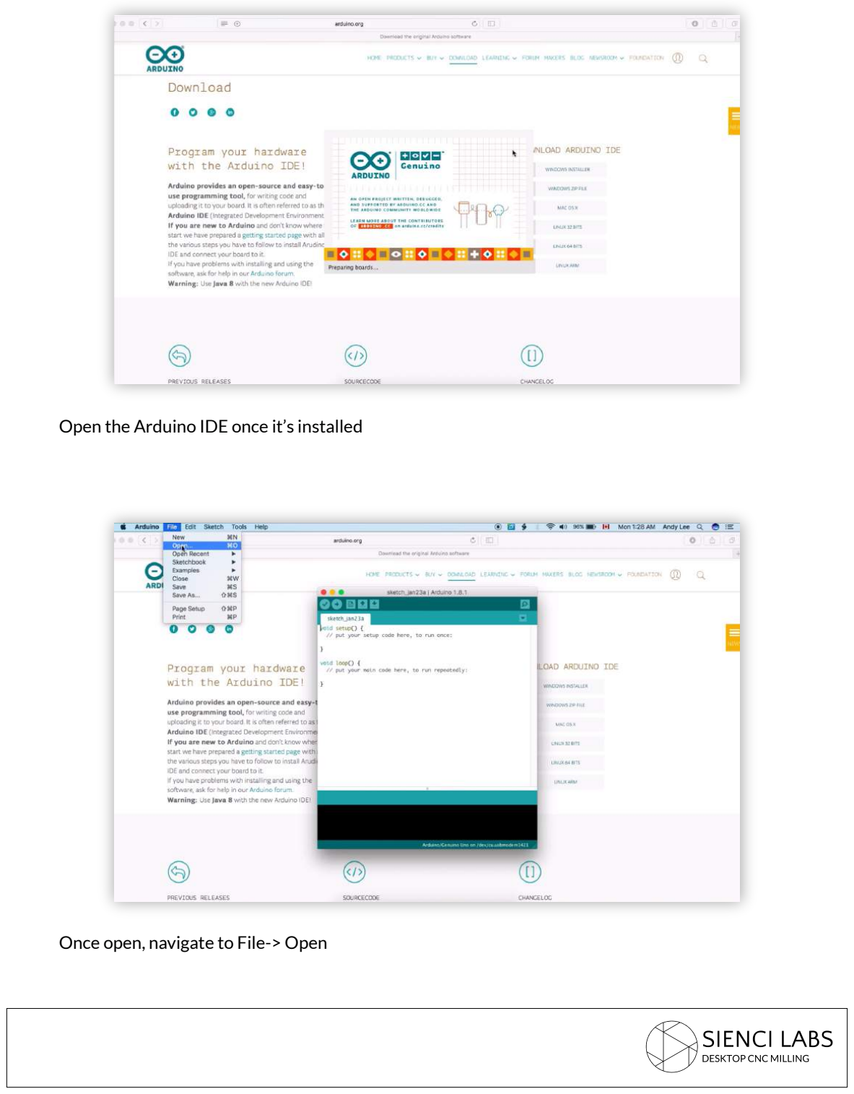
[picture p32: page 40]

Open the Arduino IDE once it’s installed

Once open, navigate to File-> Open

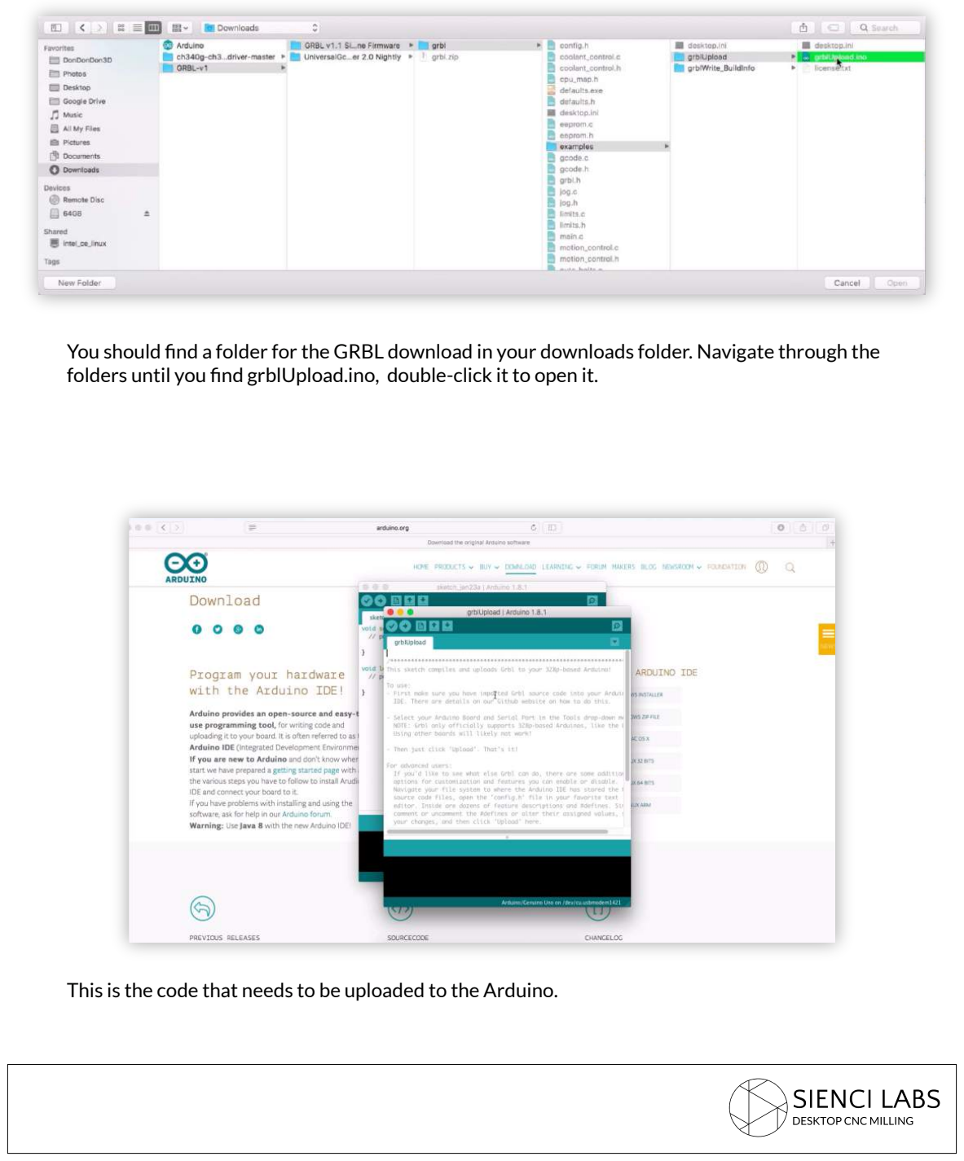
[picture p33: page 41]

You should find a folder for the GRBL download in your downloads folder. Navigate through the folders until you find grblUpload.ino, double-click it to open it.

This is the code that needs to be uploaded to the Arduino.

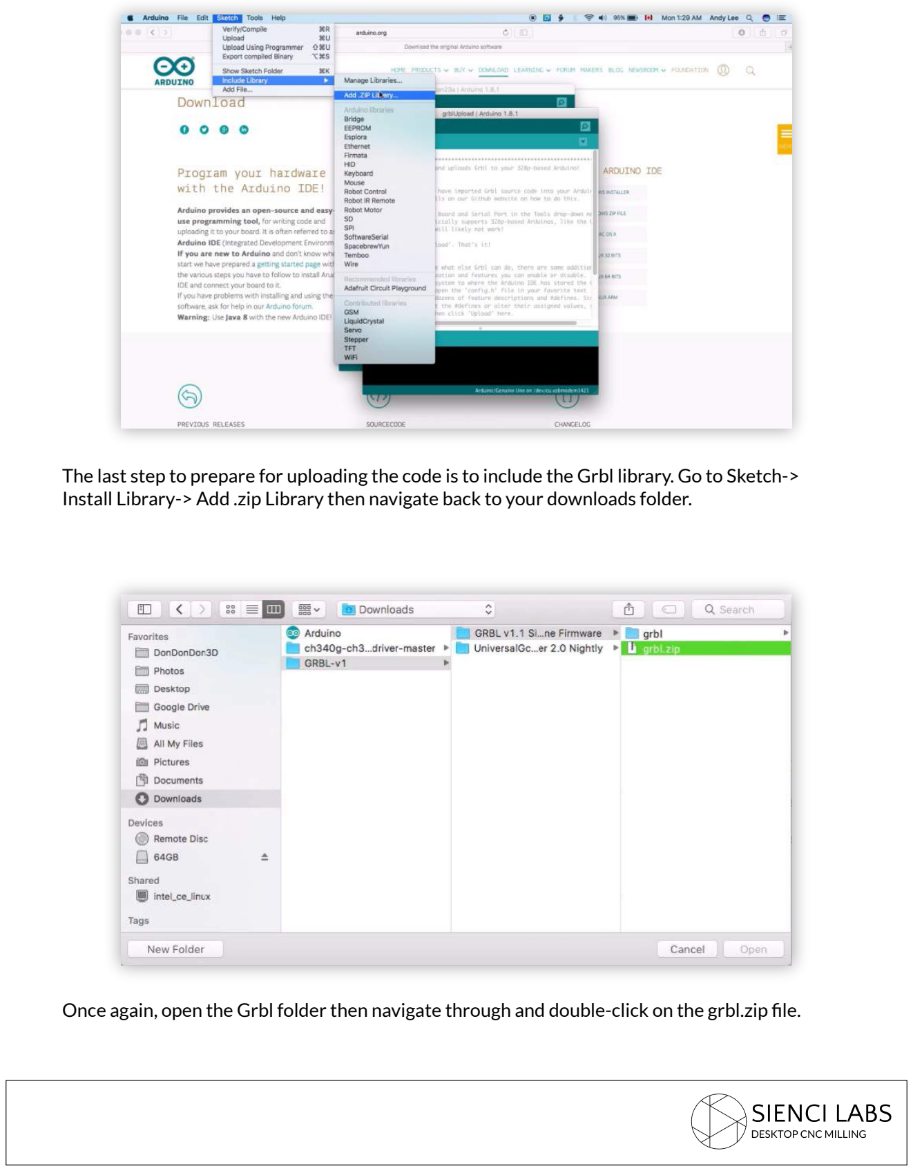
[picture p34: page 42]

The last step to prepare for uploading the code is to include the Grbl library. Go to Sketch-> Install Library-> Add .zip Library then navigate back to your downloads folder.

Once again, open the Grbl folder then navigate through and double-click on the grbl.zip file.

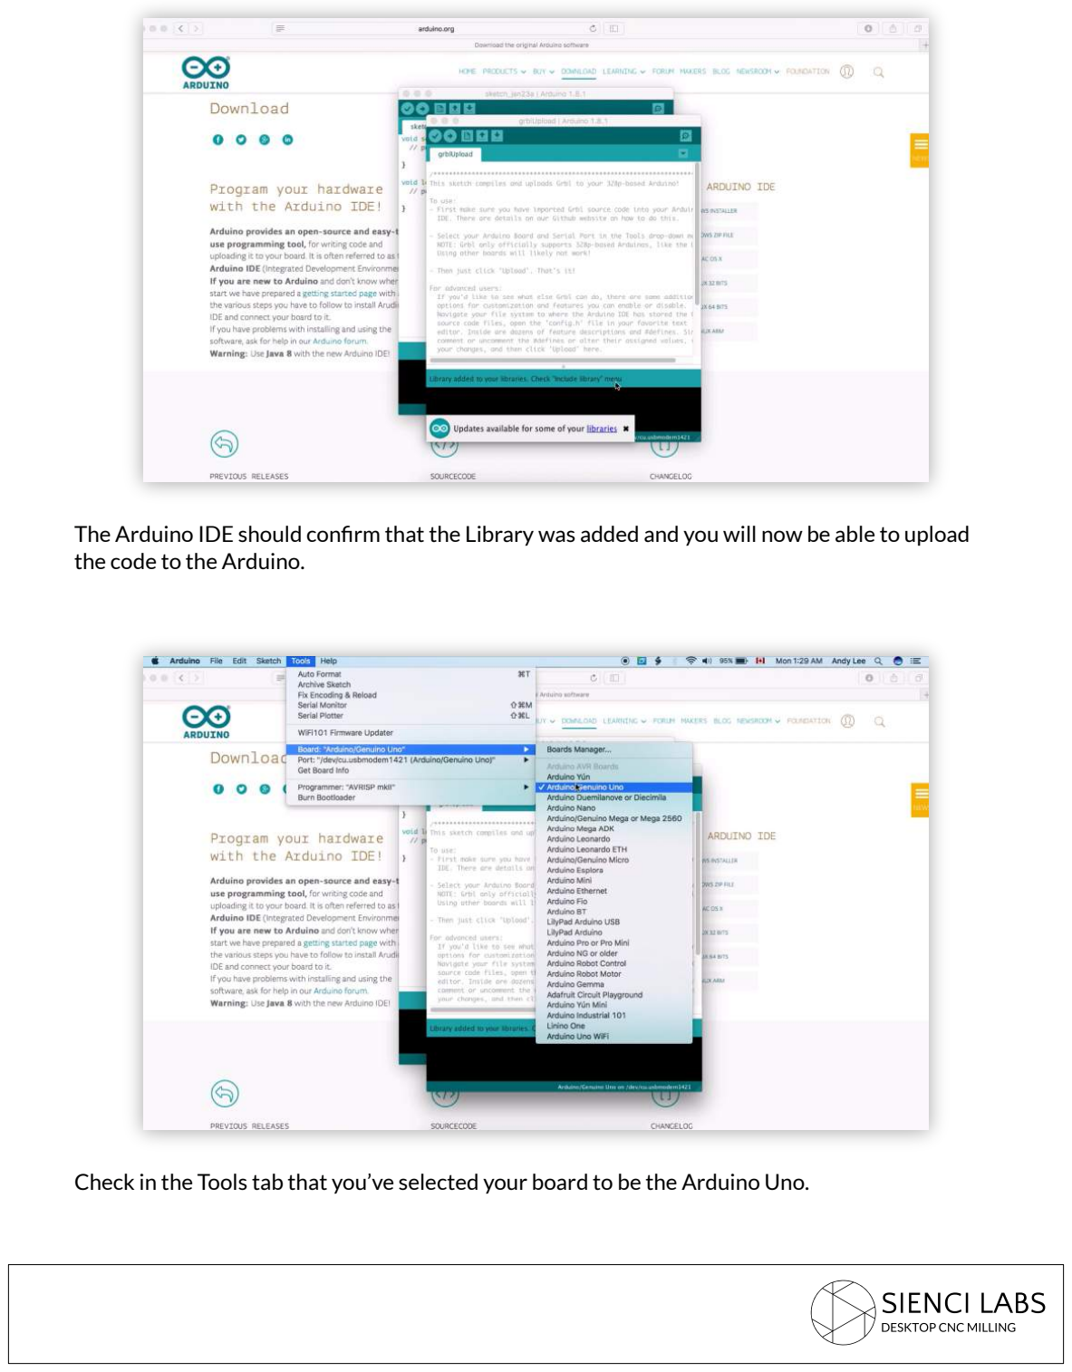
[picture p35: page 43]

The Arduino IDE should confirm that the Library was added and you will now be able to upload the code to the Arduino.

Check in the Tools tab that you’ve selected your board to be the Arduino Uno.

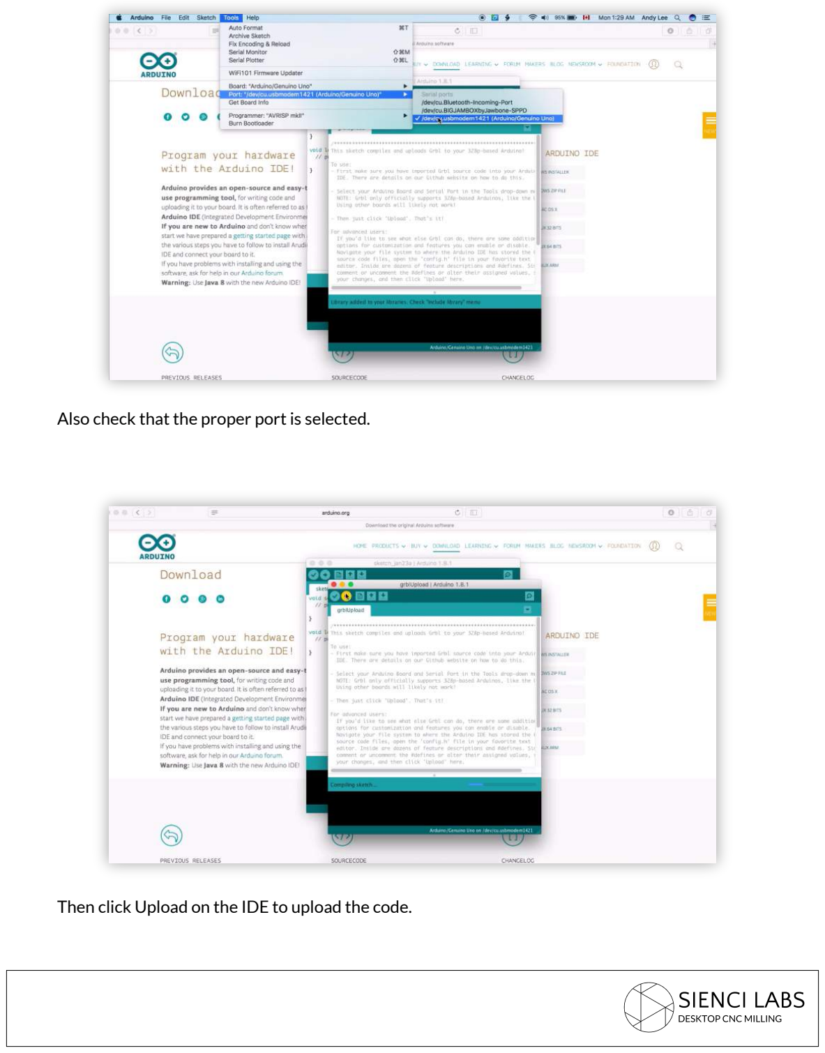
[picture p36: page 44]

Also check that the proper port is selected.

Then click Upload on the IDE to upload the code.

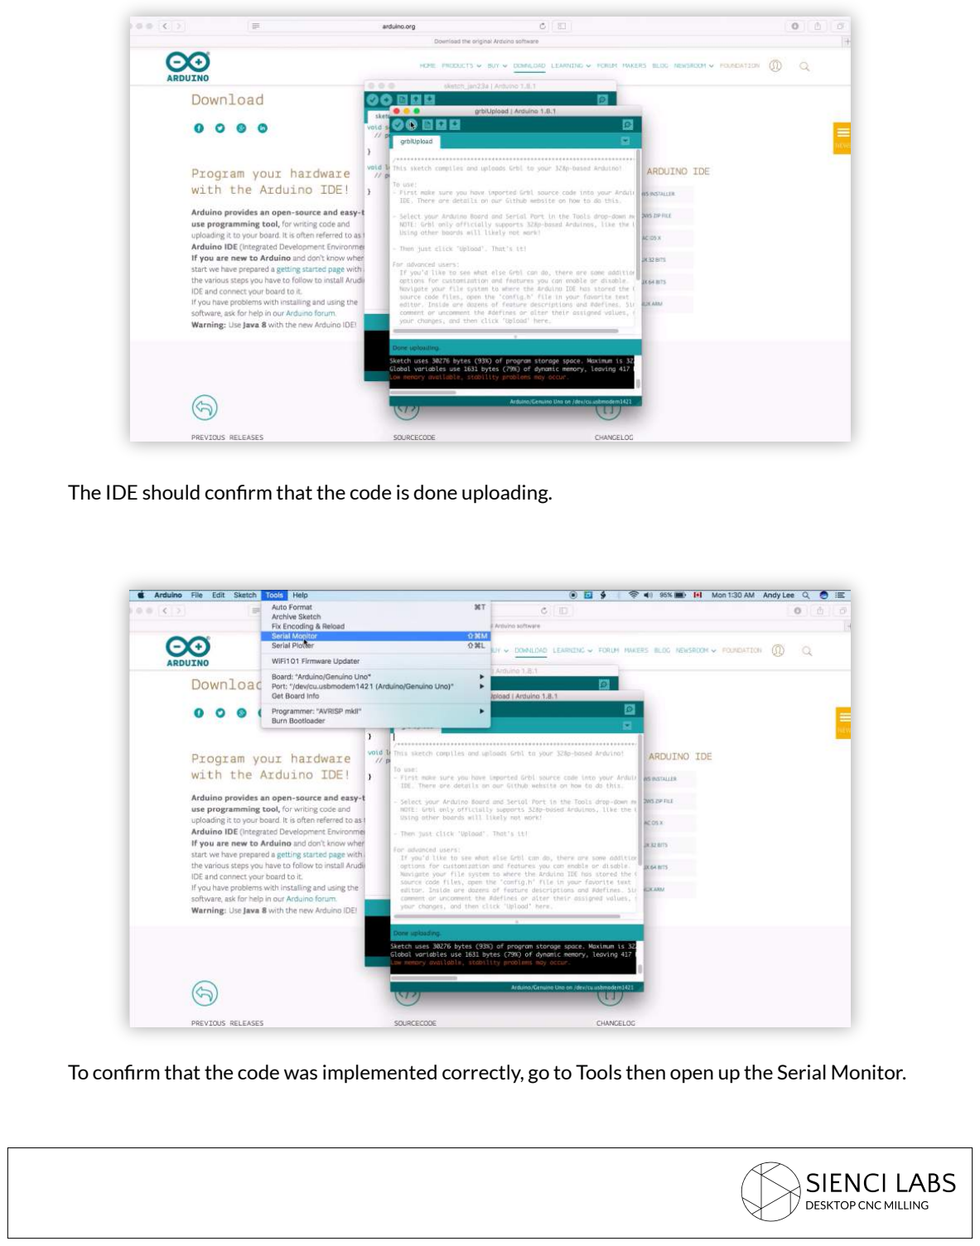
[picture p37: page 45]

The IDE should confirm that the code is done uploading.

To confirm that the code was implemented correctly, go to Tools then open up the Serial Monitor.

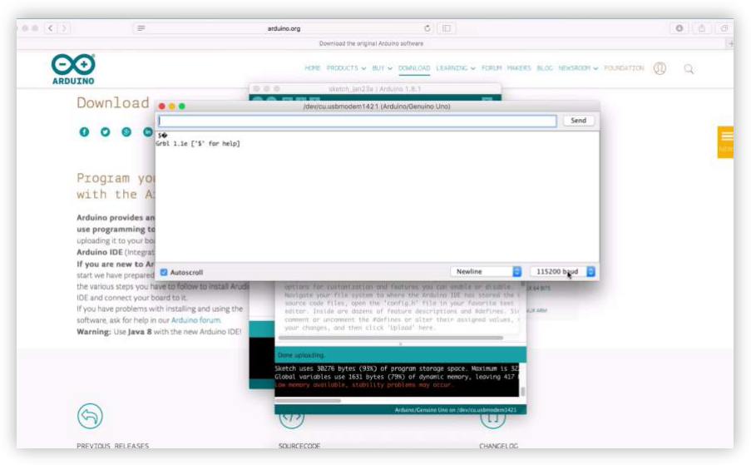
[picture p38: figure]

Once you set your baud rate to 115200 you should see that the monitor shows the following message, this means that the firmware has been uploaded correctly.

Your Mill One should now be ready to go. In order to start using your machine you should start becoming comfortable with a CAM software as well as find a program which will send the g-code to your machine. For our software recommendations, you can navigate back to the Software heading on the Resources page of our website. For additional resources, be sure to check out our other hardware resources as well as request to join our user Facebook group where you can ask questions, find answers, and interact with the rest of the Sienci community.

## Congratulations!

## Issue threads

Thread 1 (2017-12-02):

Electronics enclosure needs to be modified for 4mm frame

rsre, 2017-12-02:
Previous frame was thicker, needs to be modified to fit over 4mm frame.

rsre, 2017-12-13:
Fixed STL was uploaded.

Closed 2017-12-13.

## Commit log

2017-12-02 First push
    Added cut files, 3d print files, manual, and edited readme
    [BoM.csv, Sienci_Mill_One_V2_ACME_Nut_Mount.stl, Sienci_Mill_One_V2_Angle_Bracket.stl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]
2017-12-02 Added marked front panel
    Also fixed minor typo in readme
    [front_aetel.dxf]
2017-12-13 Added Electronics enclosure
    Fixed for 4mm chasis thickness
    AETEL branded
    [AETEL_Electronics_enclosure.stl]
2019-01-21 Added Tom Sanladerer Makita mount
    [Makita-Ridgid Router Mount.stl]
2019-01-29 Added laser cutable Y gantry
    Cleaned up directories
    [XZ_gantry.dxf, Y_Gantry.dxf, back.dxf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]
2019-01-31 Added drawings to Y gantry
2019-01-31 Original Y gantry is 25x20 but we only had 20x20 pieces of mdf to cut from
    [Y_Gantry.dxf]
